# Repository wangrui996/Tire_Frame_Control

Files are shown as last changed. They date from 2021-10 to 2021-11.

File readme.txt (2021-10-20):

引脚分配
/********** 485通信 **************
PA2(USART2_TX)----------------485_RXD
PA3(USART2_RX)--------------- 485_TXD
PB8---------------------------------485_DIR

/********** 丝杠-86----驱动器 端口定义 **************
PE5------------------------------------------------------------DIR_OUT_2(丝杆方向)
PE6------------------------------------------------------------EN_OUT_2(86驱动器使能)
PC7 (TIM8_CH2)--------------------------------------------PUL_OUT_2(脉冲)

/********** 底盘-57----驱动器 端口定义 **************
PE3------------------------------------------------------------ DIR_OUT_1 
PE4------------------------------------------------------------ EN_OUT_1
PE11(TIM1_CH2)-------------------------------------------PUL_OUT_1

/********** 位移传感器**************
PA6(Timer3_CH1)------------------------------- WXY31_A_OUT编码器A相
PA7(Timer3_CH2)------------------------------- WXY31_B_OUT编码器B相

/********** 压力采样**************
PA5(ADC1_IN5)-----------------------------------DYLF_102_OUT

/********** 锂电池电压采样**************
PA4(ADC2_IN4)-----------------------------------Li_BATTERY_OUT

/********** 电机通断控制**************
PD8--------------------------------------- ----- ----MOTOR1_POWER_CTRL
PD9-------------------------------------------------MOTOR2_POWER_CTRL

编码器初始化。定时器设置上下拉问题
motor1.c    TIM_UpdateRequestConfig(TIM1,TIM_UpdateSource_Regular); /********* 设置只有计数溢出作为更新中断 ********/
motor1.c    TIM_SelectOnePulseMode(TIM8,TIM_OPMode_Single);/******* 单脉冲模式 **********/

上下位机通信说明-------485通信
需要发送的数据：压力值--保留两位小数---两位u8数据       整数部分最大150<255, 小数两位最大99<255
                锂电池电压--保留两位小数---两位u8数据   整数部分最大150<255, 小数两位最大99<255
				丝杠位移值（高度）----发送脉冲数，1000mm量程最大发送脉冲10000(0.1mm/脉冲)---两位u8数据
				速度--后面考虑
				RS485_TX_BUF[10]=[237, 13, 255, 240, 0, 0, 0, 0, 0, 0];

需要接收的数据：  0xED 
				  0x09 
				  0x57 
				  0x21
                  指令：1/2/3/4/5/6 
				  丝杠距离高位：
				  丝杠距离低位：
				  丝杠速度：				  
				  底盘距离高位：
				  底盘距离低位：
				  底盘速度：
				  0x57
				  0x20

嵌入式系统内部通信：信号量 
					消息邮箱  
					消息队列

电机控制  底盘：指定数目、指定频率脉冲发送-----考虑添加T型加减速算法
          丝杠：要有改变方向、频率的函数
		        读取编码器脉冲函数
				M法测速函数
				PID算法实现

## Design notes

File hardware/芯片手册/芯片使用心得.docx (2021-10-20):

1、 光耦6N137、、输入电阻，一般驱动发光二极管，电流10-20mA即可，若电压为3.3V，看手册二极管正向压降1.4V，电阻阻值在R=（3.3-1.4）➗（0.01-0.02）=95-190欧，因此用100R，180R都可。Proteus仿真结果，超过380R就不导通，380R时电流大概5mA。

HCPL-2531、6N137等光耦，输入输出端的电压大小要根据实际情况判断，接单片机一端应该是3V3，接外部电路可5V。

2、 发光二极管—看最大电流、，，电压---决定限流电阻阻值

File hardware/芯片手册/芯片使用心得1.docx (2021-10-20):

芯片封装下载网站 用户名为邮箱名

1、 光耦6N137、、输入电阻，一般驱动发光二极管，电流10-20mA即可，若电压为3.3V，看手册二极管正向压降1.4V，电阻阻值在R=（3.3-1.4）➗（0.01-0.02）=95-190欧，因此用100R，180R都可。Proteus仿真结果，超过380R就不导通，380R时电流大概5mA。

HCPL-2531、6N137等光耦，输入输出端的电压大小要根据实际情况判断，接单片机一端应该是3V3，接外部电路可5V。

光耦隔离的特点：实现信号的传递（单向），而两组信号件没有电气连接，两端实现完全的电隔离，因此两端不应共电源。（因为有些噪声会延着VCC或GND传播）

B0505S电源隔离模块，推荐电路见产品详情页或数据手册。

有些场合光耦可能实现电平转换的作用（可以不用三极管），此时可以共地。

2、 发光二极管—看最大电流、，，电压---决定限流电阻阻值
3、 485通信电路

SP3485芯片：

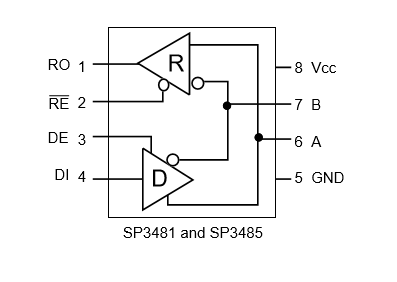
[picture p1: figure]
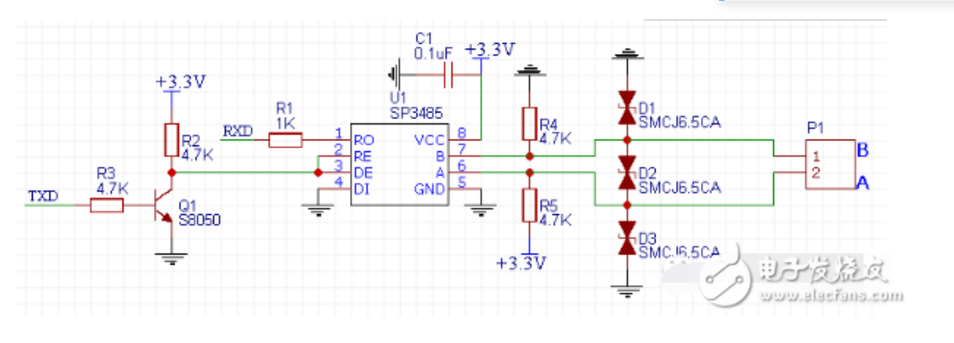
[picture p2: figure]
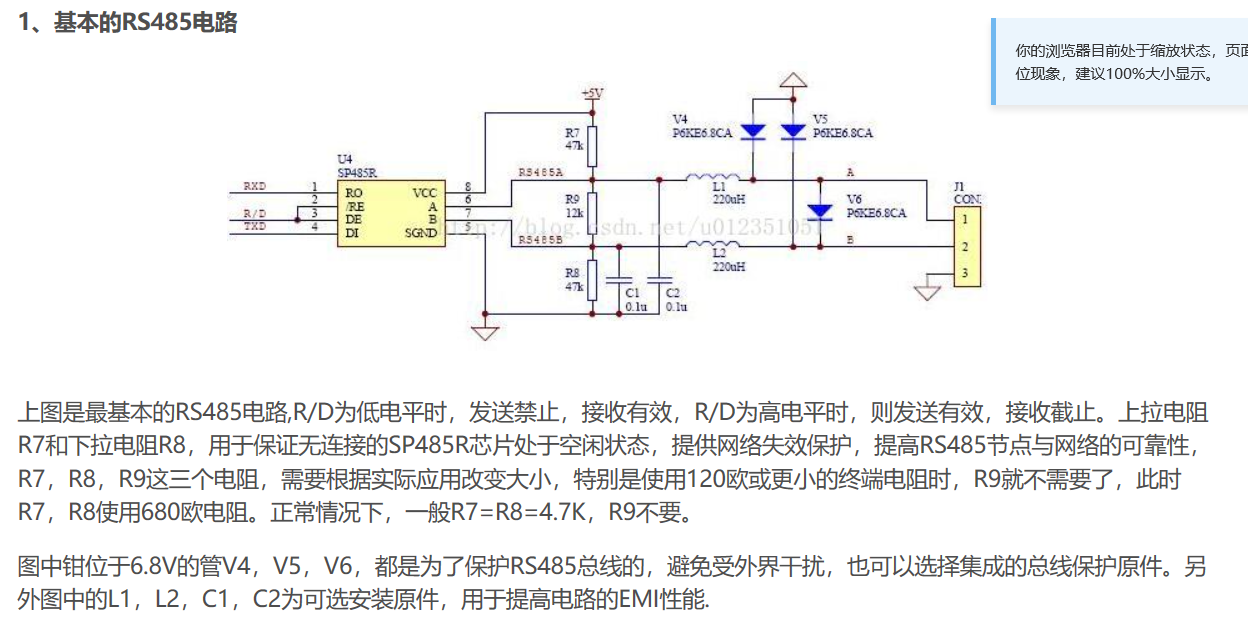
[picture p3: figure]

4、 电容应用类

滤波：

在设计电路板的时候，如果芯片没有特殊要求，需要把每个芯片旁边放上一个0.1微法电容。在PCB布线的时候，电容到电源引脚的距离最好在2mm以内。

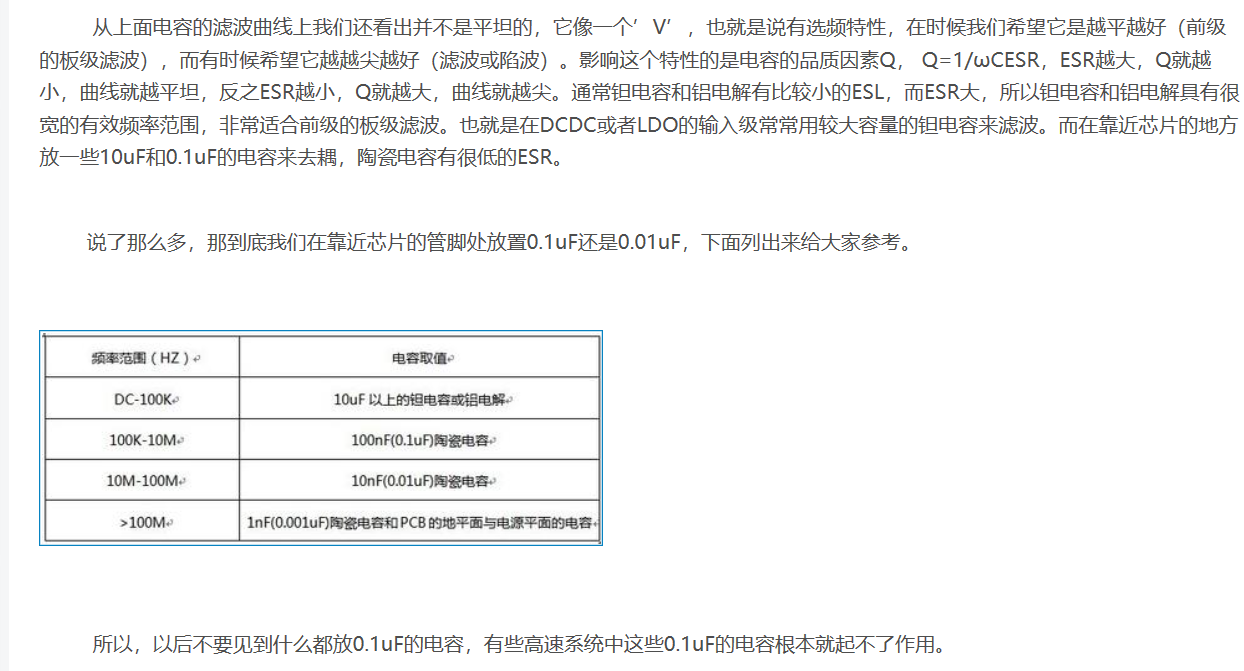
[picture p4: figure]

5、 继电器

单片机I/O口驱动能力有限、若继电器一端接地一端接I/O口，因为线圈自身电阻，单片机输出的电流不足以使触电吸合，，所以一般可用三极管如S8050方大驱动（可以用外部电压如5V、12V、24V）

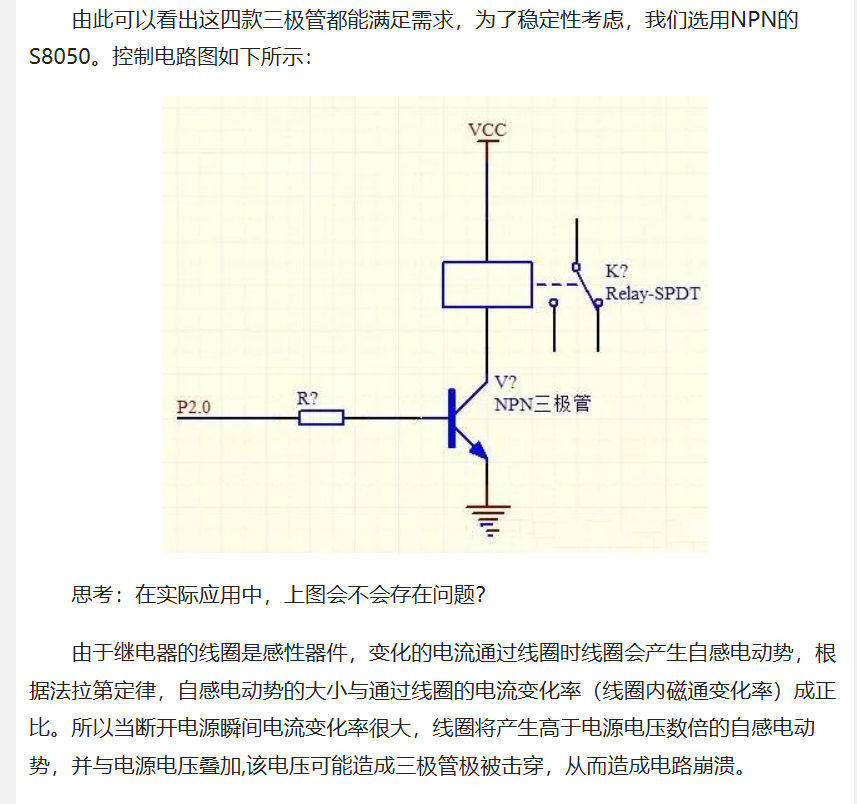
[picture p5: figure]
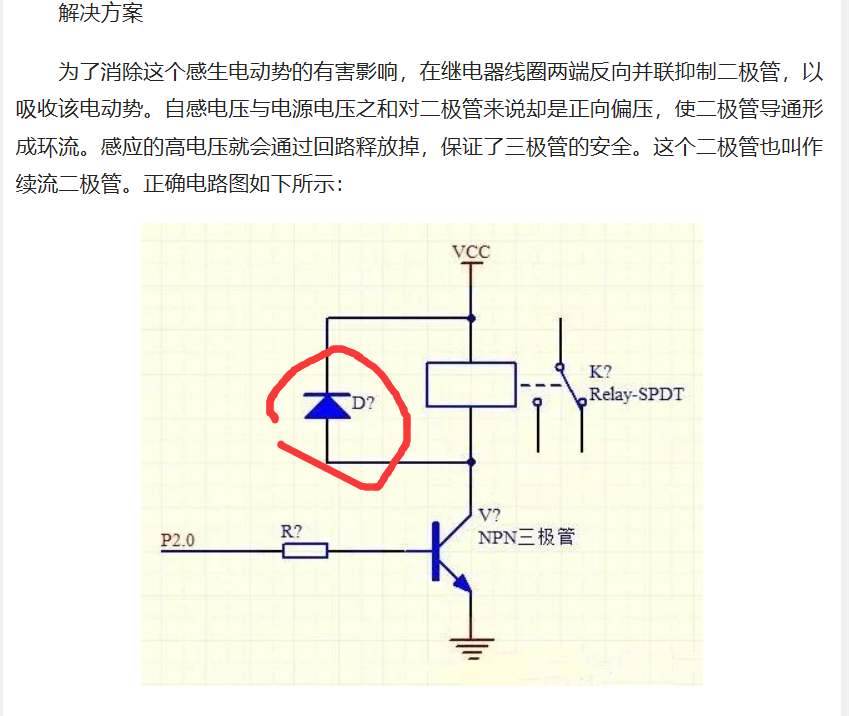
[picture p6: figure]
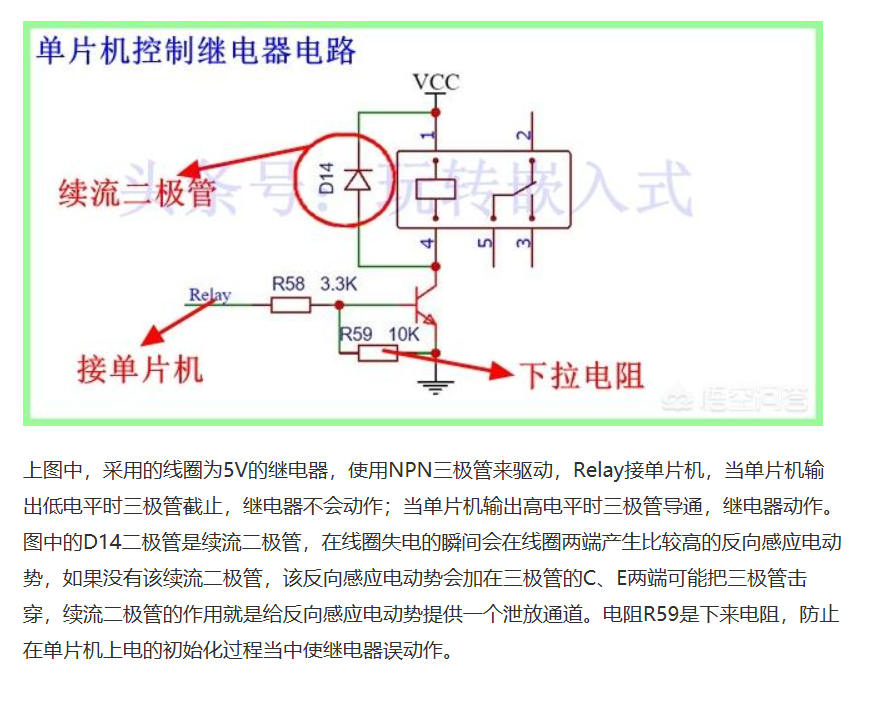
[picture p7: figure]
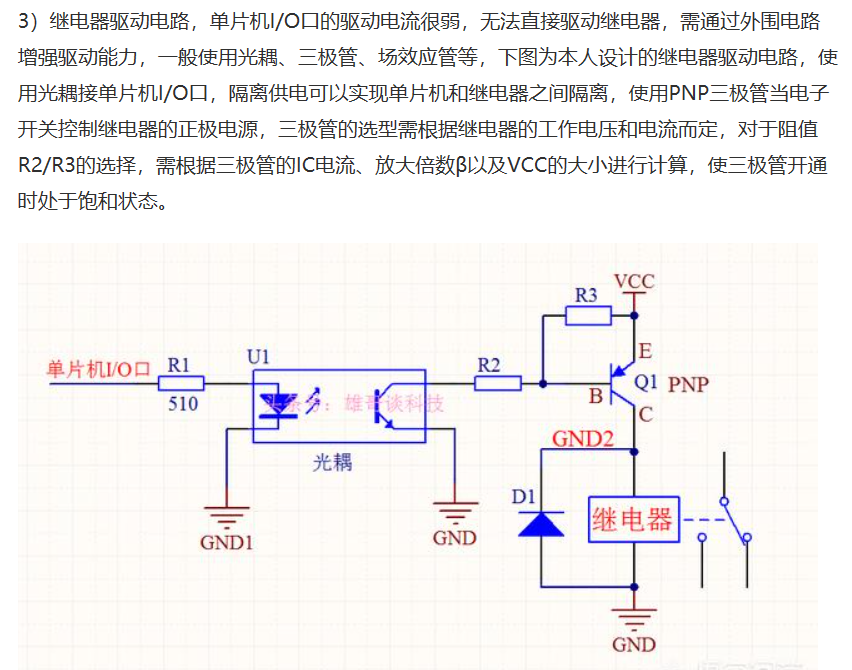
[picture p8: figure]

继电器：线圈电压怎么选，是多少？，继电器带负载能力多大，

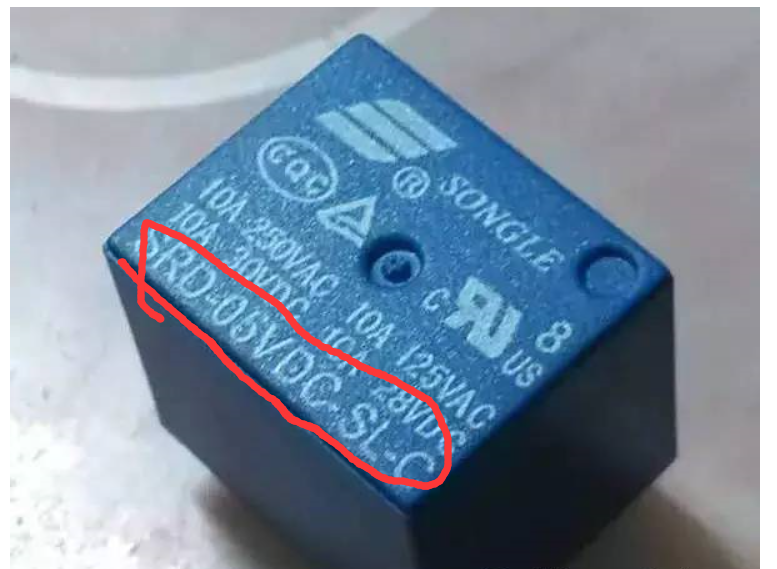
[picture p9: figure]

即可用让线圈通5V电，线圈即可吸合；

三极管：放大驱动继电器，其参数的选择？

6、 电源转换类：

5V-3.3V AMS1117

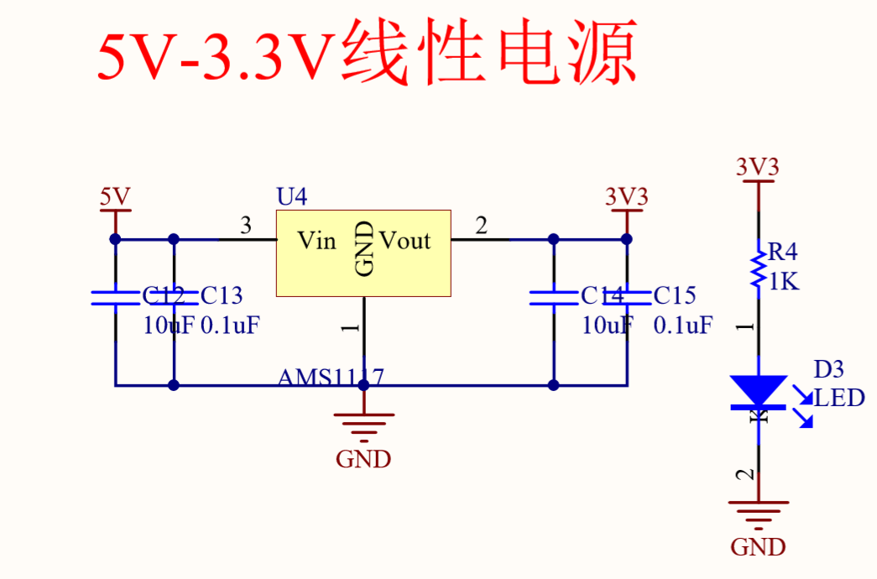
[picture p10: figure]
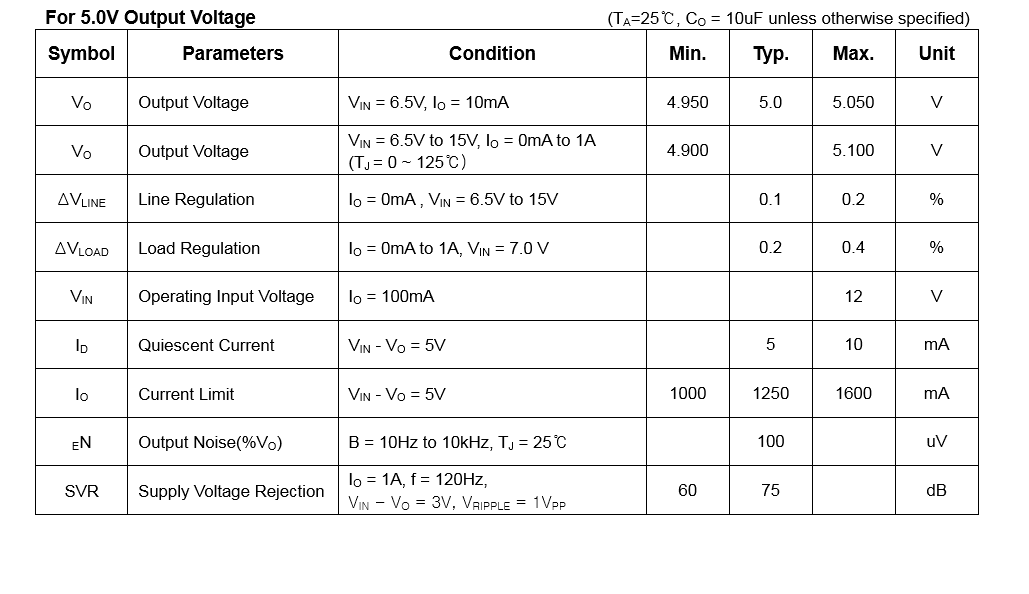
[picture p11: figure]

问题：

485电路的上下拉电阻阻值41K？、电感的大小、二极管为什么抗干扰（见第三条总结）？

位移传感器输入的电阻2K， ---换成500R，470R

继电器部分，R18的2.2K电阻怎样确定、U4光耦的VCC接的是几V？

C6和R17干啥的

继电器模块中，24V对地的滤波电容1uf？

485通信：的VCC和GND是不是也可以用隔离电源

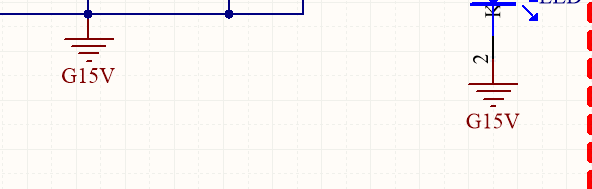
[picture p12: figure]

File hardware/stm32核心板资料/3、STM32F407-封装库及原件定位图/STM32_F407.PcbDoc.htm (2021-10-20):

Reporting Options

# File in Previous Format

Date | : | 2021/10/20
Time | : | 21:11:03
Filename | : | F:\STM32\最小系统板资料\3、STM32F407-封装库及原件定位图\STM32_F407.PcbDoc

Version | Warning
Release 12 | CAUTION - Air Gap Width previously controlled by Clearance rule is now controlled by Polygon Connect Style rule's newly introduced Air Gap Width (set to default value). Suggest reviewing each Polygon Connect Style rule's Air Gap Width attribute for correctness.
Release 13 | CAUTION - Silkscreen Over Component Pads Rules are converted to Silk To Solder Mask Clearance Rules. Suggest examining rule scopes for accuracy.

This file was generated by an earlier version of the software

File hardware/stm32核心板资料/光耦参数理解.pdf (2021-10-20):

长运通光电收集

# 光耦参数的理解

摘要：分析光耦各个指标参数的含义,以及日常设计中的注意事项,涉及 CTR 和延时。 关键字：光耦 CTR 延时

## 1 引言

光耦作为一个隔离器件已经得到广泛应用，无处不在。一般大家在初次接触到光耦时往

往感到无从下手，不知设计对与错，随着遇到越来越多的问题，才会慢慢有所体会。

本文就三个方面对光耦做讨论：光耦工作原理；光耦的 CTR 概念；光耦的延时。本讨论

也有认识上的局限性，但希望能帮助到初次使用光耦的同事。

## 1 理解光耦

光耦是隔离传输器件，原边给定信号，副边回路就会输出经过隔离的信号。对于光耦的

隔离容易理解，此处不做讨论。

以一个简单的图（图.1）说明光耦的工作：原边输入信号 Vin，施加到原边的发光二极

管和 Ri 上产生光耦的输入电流 If，If 驱动发光二极管，使得副边的光敏三极管导通，回路

VCC、RL 产生 Ic,Ic 经过 RL 产生 Vout，达到传递信号的目的。原边副边直接的驱动关联是

CTR（电流传输比），要满足 Ic≤If*CTR。

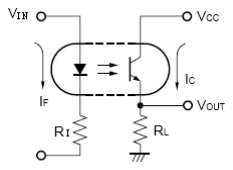
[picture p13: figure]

图.1

光耦一般会有两个用途：线性光耦和逻辑光耦，如果理解？

工作在开关状态的光耦副边三极管饱和导通，管压降<0.4V，Vout 约等于 Vcc（Vcc-0.4V

左右），Vout 大小只受 Vcc 大小影响。此时 Ic<If*CTR，此工作状态用于传递逻辑开关信号。

工作在线性状态的光耦，Ic=If*CTR，副边三极管压降的大小等于 Vcc-Ic*RL，Vout= Ic*RL

=(Vin-1.6V)/Ri * CTR*RL，Vout 大小直接与 Vin 成比例，一般用于反馈环路里面 (1.6V 是

粗略估计，实际要按器件资料，后续 1.6V 同) 。

对于光耦开关和线性状态可以类比为普通三极管的饱和放大两个状态。

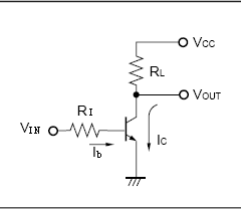
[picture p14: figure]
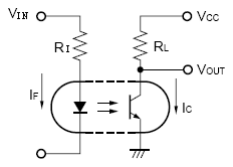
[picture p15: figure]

所以通过分析实际的电路，除去隔离因素，用分析三极管的方法来分析光耦是一个很有

效的方法。此方法对于后续分析光耦的 CTR 参数，还有延迟参数都有助于理解。

### 2 光耦 CTR

概要：1)对于工作在线性状态的光耦要根据实际情况分析；2)对于工作在开关状态的光

耦要保证光耦导通时 CTR 有一定余量；3)CTR 受多个因素影响。

## 2.1 光耦能否可靠导通实际计算

举例分析，例如图.1 中的光耦电路，假设 Ri = 1k,Ro = 1k,光耦 CTR= 50%，光耦导通

时假设二极管压降为 1.6V，副边三极管饱和导通压降 Vce=0.4V。输入信号 Vi 是 5V 的方波，

输出 Vcc 是 3.3V。Vout 能得到 3.3V 的方波吗？

我们来算算：If = (Vi-1.6V)/Ri = 3.4mA

副边的电流限制：Ic’ ≤ CTR*If = 1.7mA

假设副边要饱和导通，那么需要 Ic’ = (3.3V – 0.4V)/1k = 2.9mA，大于电流通道限

制，所以导通时，Ic 会被光耦限制到 1.7mA， Vout = Ro*1.7mA = 1.7V

比较项目 | | 光耦 | | 三极管

电路图

前级电流 | If(=(Vin-1.6)/Ri) | | Ib(=(Vin-0.6)/Ri)
电流限制条件 | Ic ≤ CTR*If | | Ic ≤β* Ib
| 理解：If 确定，光耦副边电流通道大小 确定，实际的 Ic 不能大于该通道 | | 理解：Ib 确定，三极管副边电流通道大 小确定，实际的 Ic 不能大于该通道
饱和/开关状态 | 当 RL阻值大时，Vcc/RL < CTR*If 光耦导通时，Vout ~= 0 V | | 当 RL阻值大时，Vcc/RL <β* Ib 三极管导通时，Vout ~= 0 V
放大/线性状态 | 当 RL阻值小时，Vcc/RL > CTR*If 此时，光耦副边会提高光敏三极管的导 通压降，限制实际的 Ic 在电流通道内 (Ic = CTR*If)。光耦导通时，Vout 输 出大小与 Vin 有线性关系。 | | 当 RL阻值小时，Vcc/RL >β* Ib 此时，三极管会提高管压降，限制实际 的 Ic 在电流通道内(Ic =β* Ib)。三 极管导通时，Vout 输出大小与 Vin 有线 性关系。

所以副边得到的是 1.7V 的方波。

为什么得不到 3.3V 的方波，可以理解为图.1 光耦电路的电流驱动能力小，只能驱动

1.7mA 的电流，所以光耦会增大副边三极管的导通压降来限制副边的电流到 1.7mA。

解决措施：增大 If；增大 CTR；减小 Ic。对应措施为：减小 Ri 阻值；更换大 CTR 光耦；

增大 Ro 阻值。

将上述参数稍加优化，假设增大 Ri 到 200 欧姆，其他一切条件都不变，Vout 能得到 3.3V

的方波吗？

重新计算：If = (Vi – 1.6V)/Ri = 17mA；副边电流限制 Ic’ ≤ CTR*If = 8.5mA，远

大于副边饱和导通需要的电流(2.9mA)，所以实际 Ic = 2.9mA。

所以，更改 Ri 后，Vout 输出 3.3V 的方波。

开关状态的光耦，实际计算时，一般将电路能正常工作需要的最大 Ic 与原边能提供的

最小 If 之间 Ic/If 的比值与光耦的 CTR 参数做比较，如果 Ic/If ≤CTR，说明光耦能可靠

导通。一般会预留一点余量（建议小于 CTR 的 90%）。

工作在线性状态令当别论。

## 2.2 CTR 受那些因素影响

上一节说到设计时要保证一定 CTR 余量。就是因为 CTR 的大小受众多因素影响，这些因

素之中既有导致 CTR 只离散的因素（不同光耦），又有与 CTR 有一致性的参数（壳温/If）。

1)光耦本身：以 8701 为例，CTR 在 Ta=25℃/If=16mA 时，范围是(15%~35%)
说明 8701 这个型号的光耦，不论何时/何地，任何批次里的一个样品，只要在 Ta=25℃ /If=16mA 这个条件下，CTR 是一个确定的值，都能确定在 15%~35%以内。 计算导 通时，要以下限进行计算，并且保证有余量。计算关断时要以上限。 2)壳温影响：

Ta=25℃条件下的 CTR 下限确定了，但往往产品里面温度范围比较大，比如光耦会工作

在（-5~75℃）下，此种情况下 CTR 怎么确定？还是看 8701 的手册：有 Ta-CTR 关系图：

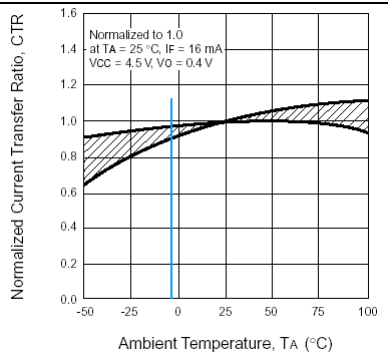
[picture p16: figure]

从图中看出，以 25 度的为基准，在其他条件不变的情况下，-5 度下的 CTR 是 25 度下

的 0.9 倍左右，75 度下最小与 25 度下的 CTR 持平。

所以在 16mA/(-5~75℃)条件下，8701 的 CTR 最小值是 15%*0.9 = 13.5%

3) 受 If 影响。

假设如果实际的 If 是 3.4mA，那么如何确定 CTR 在 If=3.4mA / Ta=(-5~75℃)条件下的

最小 CTR 值。

查看 8701 的 If-CTR 曲线。图中给出了三条曲线，代表抽取了三个样品做测试得到的

If-CTR 曲线，实际只需要一个样品的曲线即可。

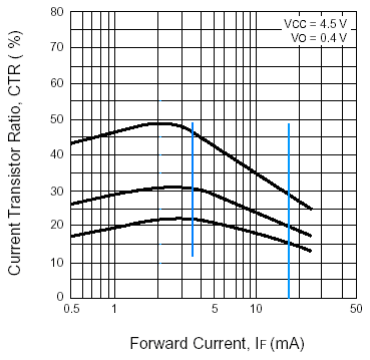
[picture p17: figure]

注：此图容易理解为下限/典型/上限三个曲线，其实不然。大部分图表曲线只是一个相

对关系图，不能图中读出绝对的参数值。

计算：选用最上面一条样品曲线，由图中查出，If=16mA 时 CTR 大概 28%，在 If=3.4mA

时 CTR 大概在 46%。3.4mA 是 16mA 时的 46%/28% = 1.64 倍；

所以，在 If=3.4mA / (-5~75℃)，CTR 下限为 13.5% * 1.64 = 22.2%

以上所有分析都是基于 8701 的，其他光耦的特性曲线需要查用户手册，分析方法一样。

## 3 光耦延时

上述 CTR 影响到信号能不能传过去的问题，类似于直流特性。下面主要分析光耦的延时

特性，即光耦能传送多快信号。

涉 及到 两个参 数： 光耦导通延时 tplh 和 光耦关断 延时 tphl ，以 8701 为例 ：在

If=16mA/Ic=2mA 时候，关断延时最大 0.8uS，导通延时最大 1.2uS。所以用 8701 传递 500k

以上的开关信号就需要不能满足。

下图是一个实测的延时波形（ch4 原边（红），ch2 副边（绿））

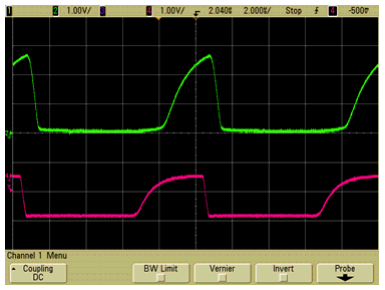
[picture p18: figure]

图.2
对于 tp 参数的设计更应该考虑余量，因为 tp 参数也受其他因素影响较多。
1) 受温度影响
8701 的 Ta-If 特征曲线：温度升高，开关延时都会增大。

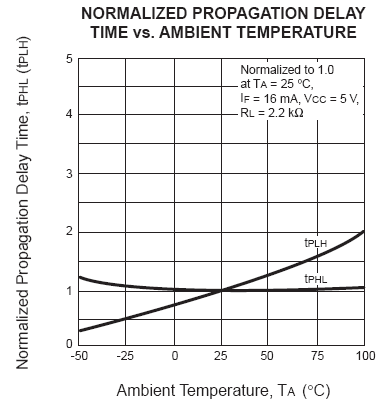
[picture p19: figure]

图.3
2) 受原边 If 大小影响
8701 的 tp-If 特征曲线：If 增大，关断延时减小，开通延时增大

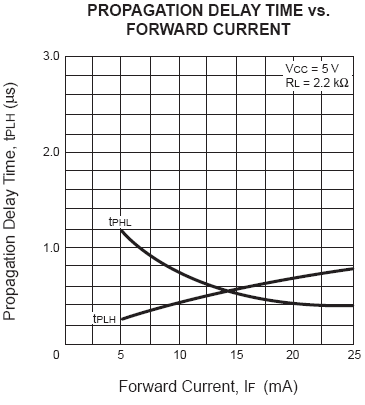
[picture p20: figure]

图.4
3) 受副边 Ic 大小影响
8701 的 tp-RL 特征曲线：RL 减小，导通延时增大明显

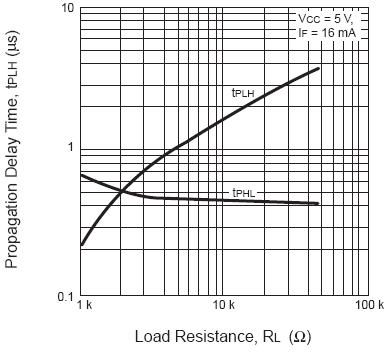
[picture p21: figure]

图.5
针对具体电路的特点，计算最大延时时也是采用与 CTR 一样的方法，通过器件资料给 定特定环境下的准确范围，然后逐一通过三个曲线确定具体电路下的光耦最大延时。

注：同一个型号的光耦 CTR/延时特性是一致的，不同光耦的延时特性不尽相同，所以 需要根据所用光耦的用户手册来确定。

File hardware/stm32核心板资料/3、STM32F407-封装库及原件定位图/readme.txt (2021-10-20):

本文件夹包含AD版本的封装库,大家根据自己的需要选择.我们不提供PROTEL之外的其他PCB软件封装库,请见谅.

	       	出品：   嵌入式开发网 
                         mcudev.taobao.com

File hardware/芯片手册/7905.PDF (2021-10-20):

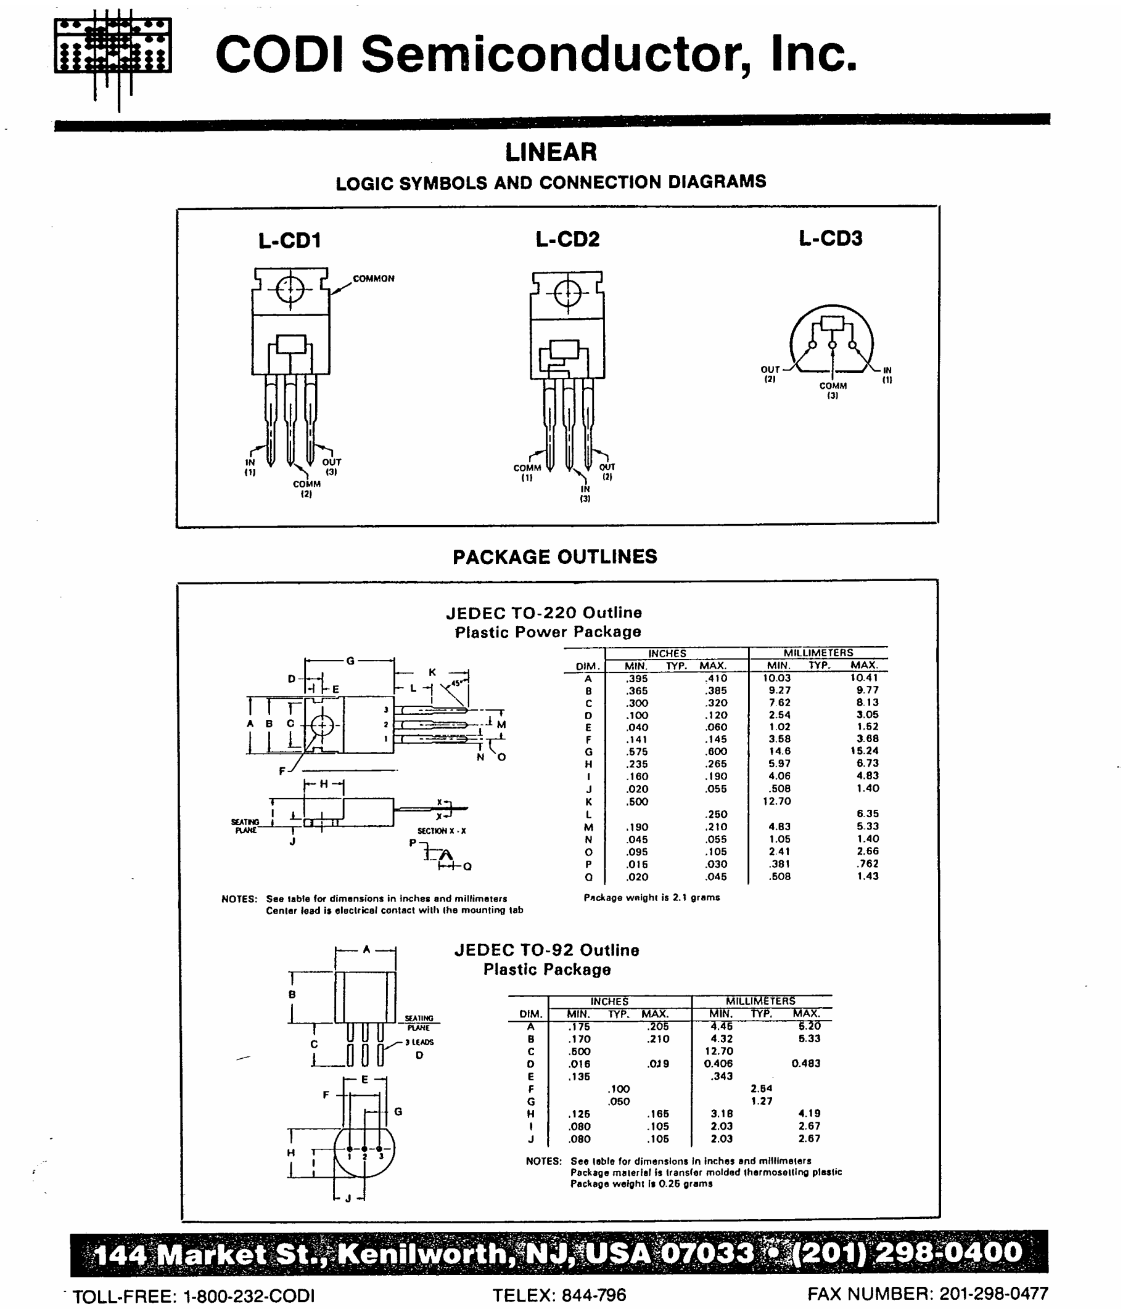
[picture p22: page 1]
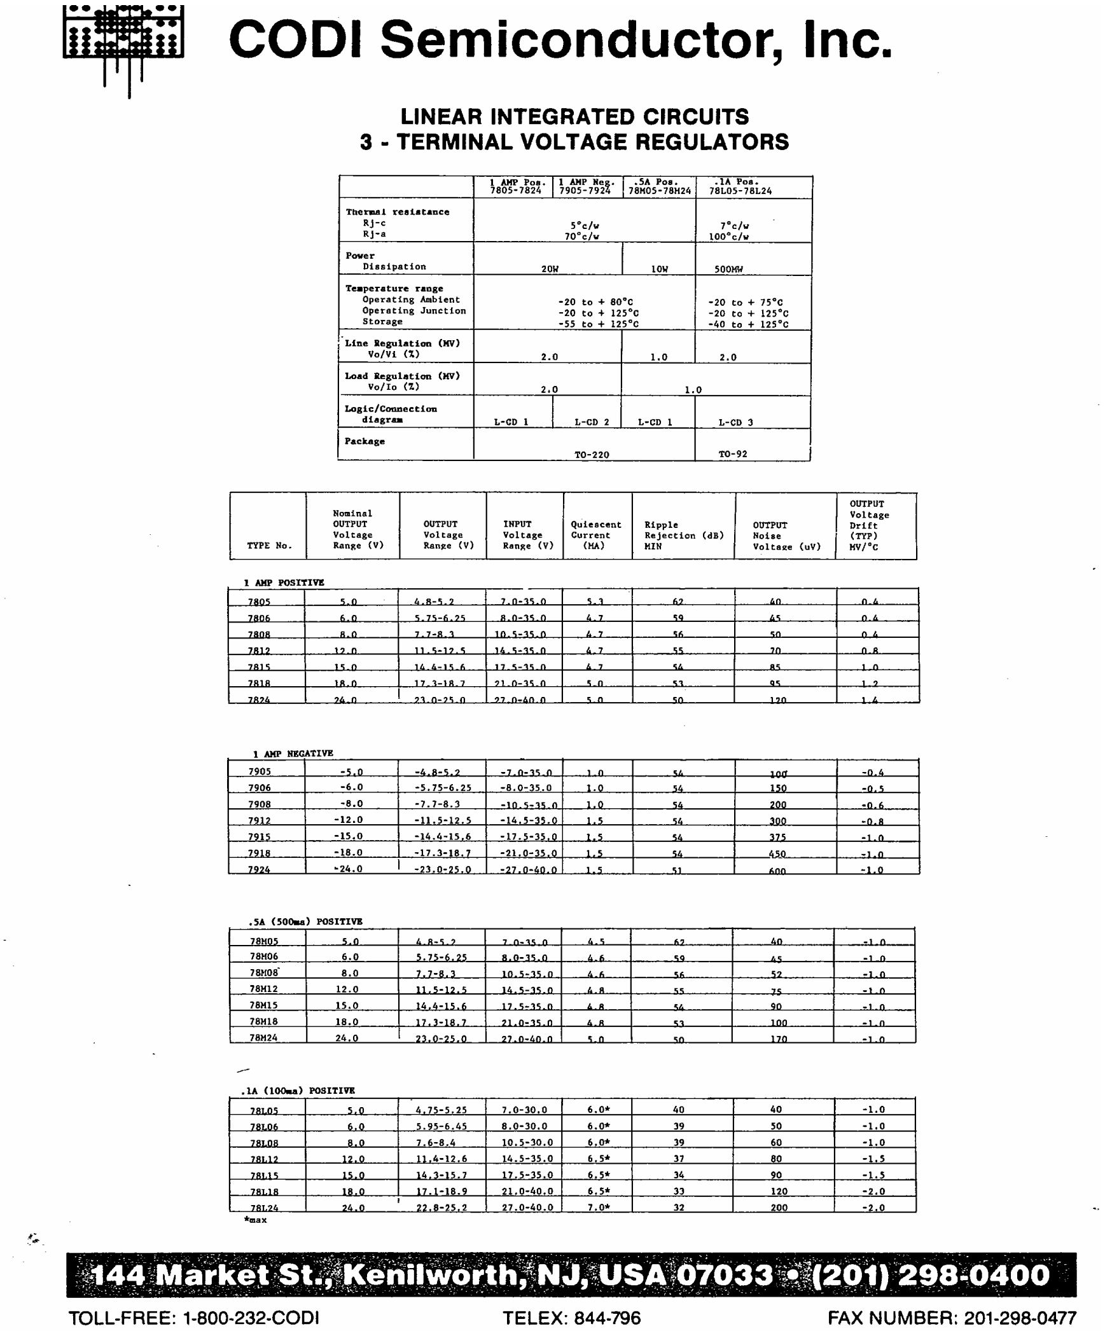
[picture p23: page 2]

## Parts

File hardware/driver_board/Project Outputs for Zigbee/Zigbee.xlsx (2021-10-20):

Comment | Description | Designator | Footprint | LibRef | Quantity | 购买链接 | 备注
F407VGT6底座封装 |  | 1 | F407VGT6底座封装 | F407VGT6底座封装 | 1
1uF | Capacitor | C6, C8, C11, C12 | 0603_C | CAP | 4 | https://item.taobao.com/item.htm?spm=a1z10.3-c-s.w4002-18137167944.16.2e192ec8RxSewg&id=530610812107 | 电阻电容直接买一个包就行
0.1uF | Capacitor | C13 | 0603_C | CAP | 1
LED | LED 发光二极管 | D1, D2, D3, D4, D6, D7, D10, D11, D15, D16 | 0603_LED | LED | 10 | https://item.taobao.com/item.htm?spm=a1z10.3-c-s.w4002-18137167944.15.dc9c2ec8fDyNGL&id=525875387129 | LED也是一个包各种颜色都有
LED红 | LED 发光二极管 | D5, D12 | 0603_LED | LED | 2
MMBD7000 |  | D9, D14 | SOT23 | MMBD7000 | 2 | https://item.taobao.com/item.htm?spm=a1z10.3-c-s.w4002-18137167944.9.618d2ec85Wt529&id=611336762473
holes |  | H1, H2, H3, H4 | 铜柱（小焊盘） | 铜柱 | 4
COM_2 |  | J1, J2, J3, J4, J5, J6, J7, J8, J9, J10, J11, J12, J13, J14, J15 | 5.08A-2PIN | COM_2 | 15 | https://item.taobao.com/item.htm?spm=a1z10.3-c-s.w4002-18137167944.12.22982ec8x13a8i&id=538793070757
header |  | JP6 | 5.08A-3PIN | HEADER 3 | 1
OJ-SS-124HM2 |  | K1, K2 | G4A-1A-PE-24V | OJ-SS-124HM2 | 2 | https://item.taobao.com/item.htm?spm=a1z09.2.0.0.40a52e8dBBcYpT&id=20355564384&_u=l1k54e5p1c41
NPN2 | 贴片 | Q1, Q2 | SOT-23-3 | NPN2 | 2 | https://item.taobao.com/item.htm?spm=a1z10.3-c-s.w4002-18137167944.21.6c652ec8VVapCy&id=611258987843
20K | Resistor | R1 | 0603_R | RES | 1
2K | Resistor | R2, R3, R13, R14, R17, R25, R31, R35 | 0603_R | RES | 8
10K | Resistor | R4 | 0603_R | RES | 1 | https://item.taobao.com/item.htm?spm=a1z10.3-c-s.w4002-18137167944.12.515b2ec820JMOL&id=530584393475 | 电阻电容单买也行，就是要一个一个找，都在一家店 (https://item.taobao.com/item.htm?spm=a1z10.3-c-s.w4002-18137167944.12.515b2ec820JMOL&id=530584393475)
180R | Resistor | R5, R6, R10, R16, R19, R23 | 0603_R | RES | 6
100K | Resistor | R7 | 0603_R | RES | 1
1K | Resistor | R8, R9, R12, R20, R21, R22, R27, R28, R32, R38 | 0603_R | RES | 10
5K | Resistor | R11 | 0603_R | RES | 1
470R | Resistor | R15, R24 | 0603_R | RES | 2
2.2K | Resistor | R18, R26 | 0603_R | RES | 2
4.7K | Resistor | R29, R30 | 0603_R | RES | 2
100R | Resistor | R33, R34, R37 | 0603_R | RES | 3
120R | Resistor | R36 | 0603_R | RES | 1
HCPL-2531 |  | U1, U3, U7 | SOP8 | HCPL-2531 | 3 | https://item.taobao.com/item.htm?spm=a1z10.3-c-s.w4002-18137167944.9.c8e62ec8I7sJBd&id=534341592457
6N137 |  | U2, U5 | SOP8 | 6N137 | 2 | https://item.taobao.com/item.htm?spm=a1z10.3-c-s.w4002-18137167944.9.7b1b2ec8Sd4msu&id=534092834069
TLP185 |  | U4, U6 | SOP4 | TLP184 | 2 | https://item.taobao.com/item.htm?spm=a1z10.3-c-s.w4002-18137167944.9.5d642ec8Y6uTDr&id=597007341875
MAX485ESA |  | U8 | SOP8 | MAX485ESA | 1 | https://item.taobao.com/item.htm?spm=a1z10.3-c-s.w4002-18137167944.9.55722ec8YVXSXd&id=527232535941

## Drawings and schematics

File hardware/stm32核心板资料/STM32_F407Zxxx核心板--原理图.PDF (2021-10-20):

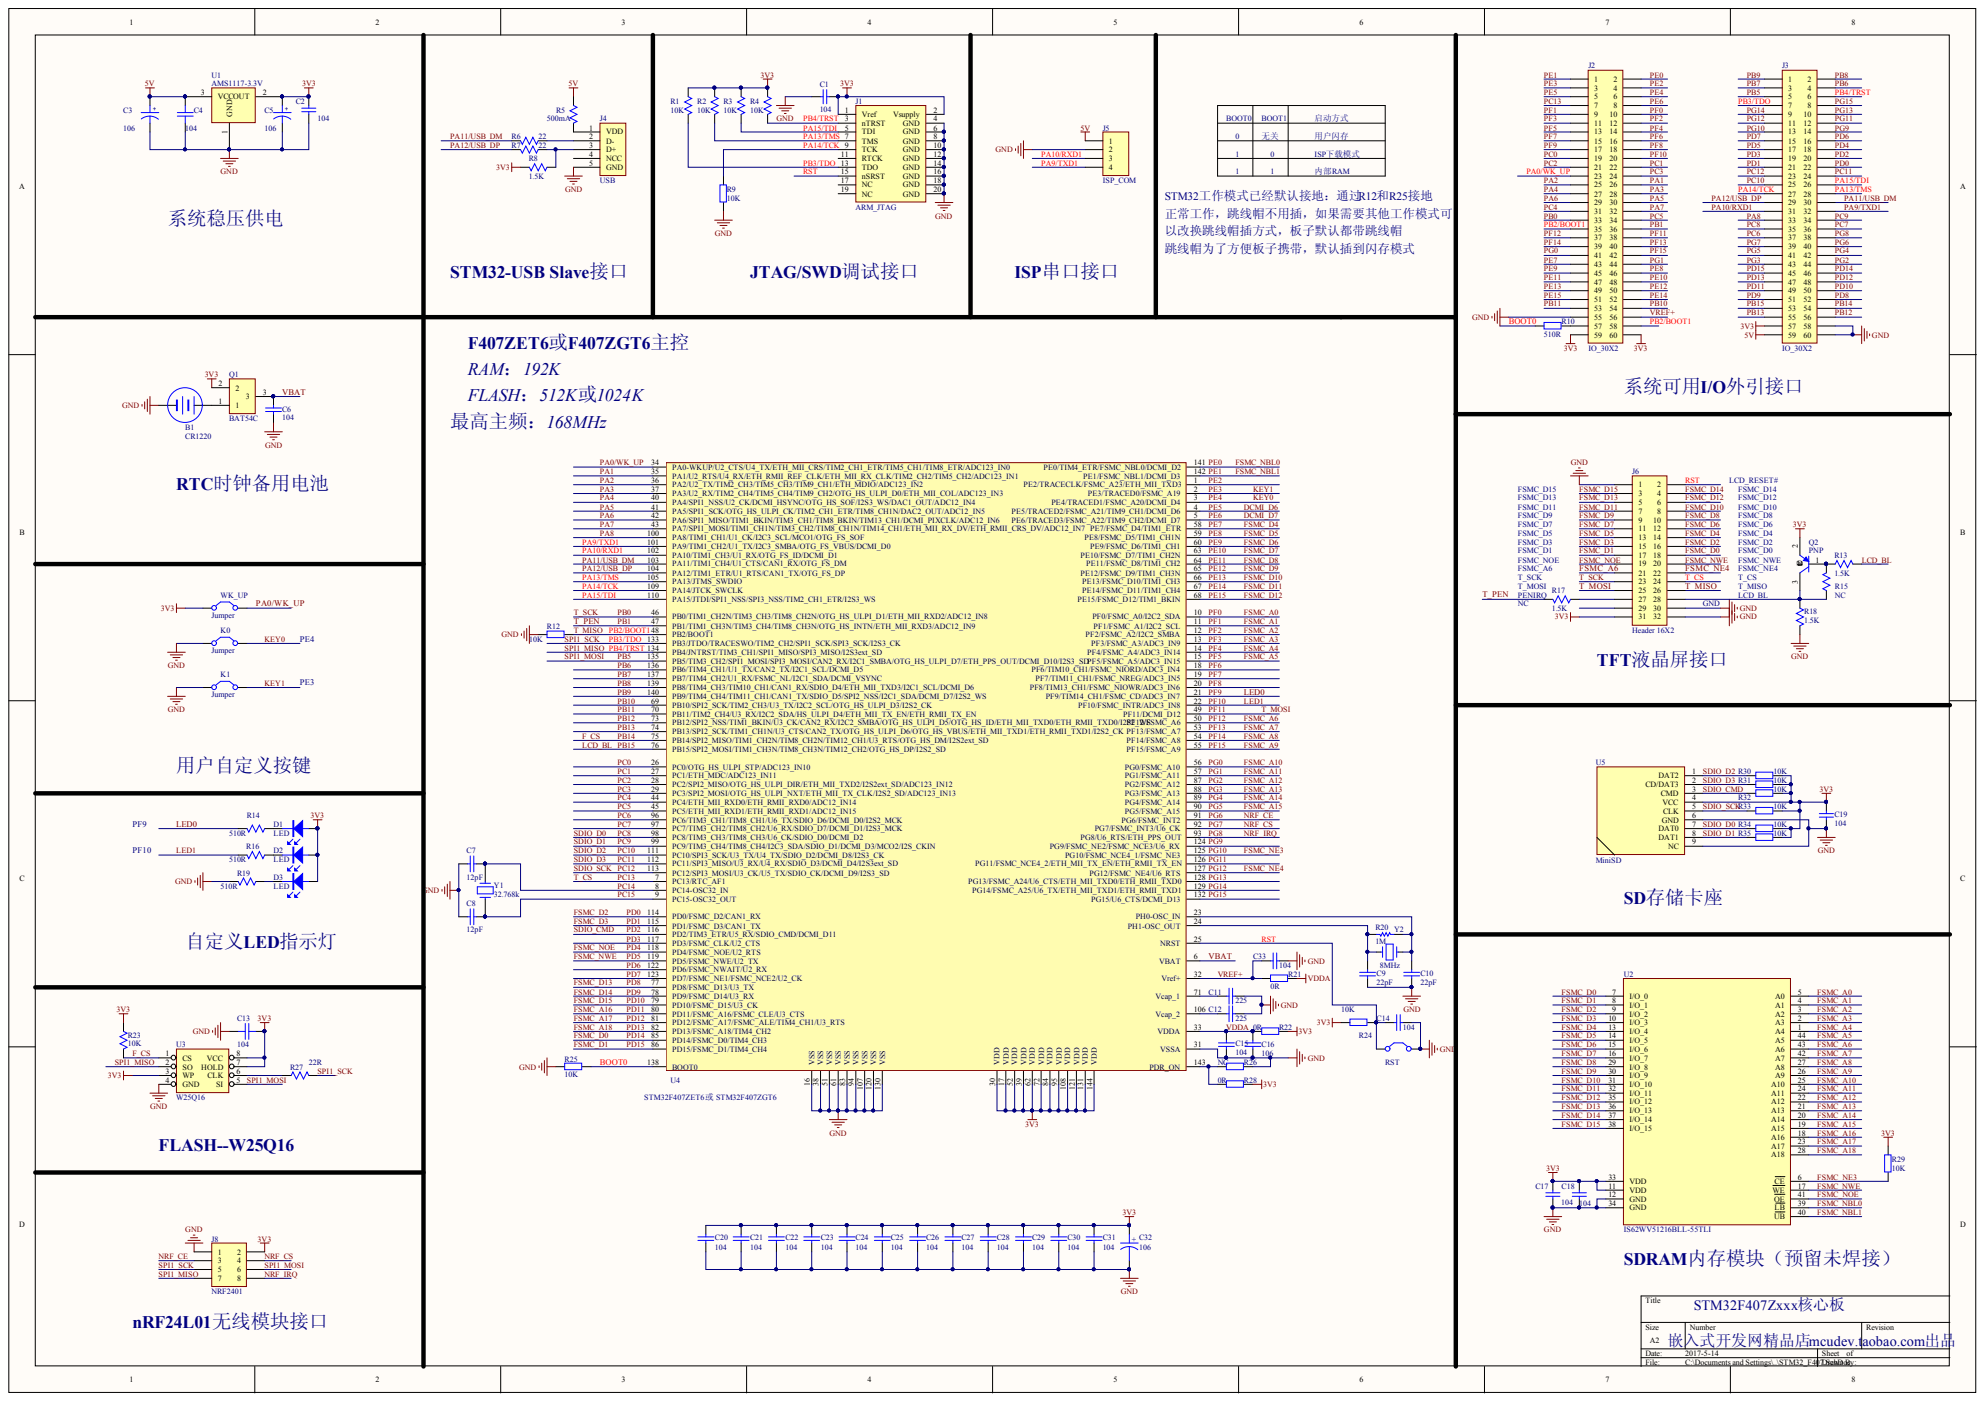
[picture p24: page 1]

PA15/TDI PB3/TDO PB4/TRST RST

VRE F + | 8MHz C 9

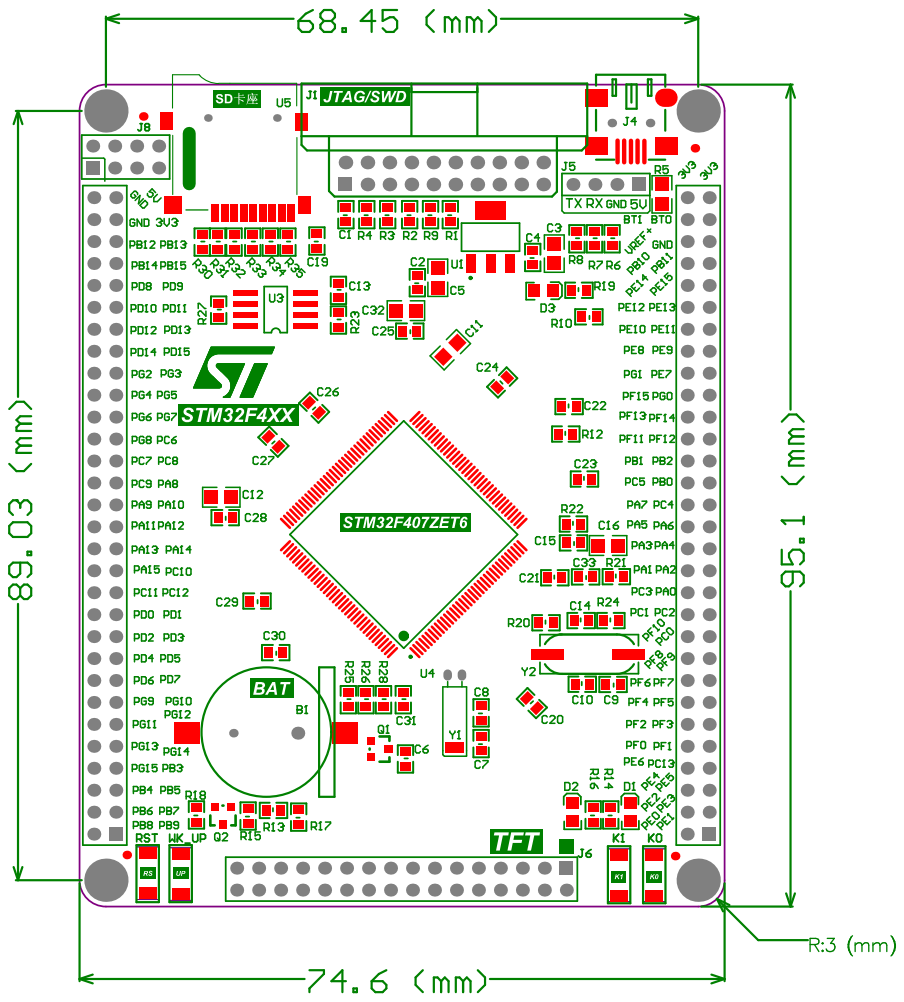
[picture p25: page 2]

Bill of Materials | <Parameter Title not found>
Source Data From: | STM32_F407.PrjPCB
Project: | | STM32_F407.PrjPCB
Variant: | | None
Creation Date: 2017-5-14 | 16:17:47
Print Date: | 42869 | 42869.67907
Footprint | Comment | LibRef | Designator | Description | Quantity
CP1220 | CR1220 | BATTERY | B1 | 1
RC0603 | 104 | Cap, Cap, CAP,
CAP, CAP, CAP,
CAP, Cap, Cap,
Cap Semi, CAP,
CAP, CAP, CAP,
CAP, CAP, CAP,
CAP, CAP, CAP,

## CAP, CAP, CAP

C1, C2, C4, C6, C13, C14, C15, C17, C18, C19, C20, C21, C22, C23, C24, C25, C26,

## C27, C28, C29, C30, C31, C33

Capacitor, Capacitor, [NoValue], Capcitor, [NoValue], Capcitor, Capcitor, Capacitor,

## Capacitor, Capacitor (Semiconductor SIM

Model), Capcitor, Capcitor, Capcitor, Capcitor, Capcitor, Capcitor, Capcitor, Capcitor, Capcitor, Capcitor, Capcitor,

## Capcitor, Ca

23

RC0805 | 106 | CAP2, CAP2,
CAP,

## CAPACITOR POL

C3, C5, C16, C32 | [NoValue], [NoValue], Capcitor, Capacitor | 4
RC0603 | 12pF | CAP | C7, C8 | Capcitor | 2
RC0603 | 22pF | CAP | C9, C10 | Capcitor | 2
RC0805 | 225 | CAP | C11, C12 | Capcitor | 2
LED0805 | LED | LED | D1, D2, D3 | | 3
JTAG20P | ARM_JTAG | JTAG | J1 | JTAG | 1
IDE2X30 | IO_30X2 | Header 30X2 | J2, J3 | Header, 30-Pin, Dual row | 2
MINUSB | USB | usb | J4 | | 1
HDR1X4 | ISP_COM | Header 4 | J5 | Header, 4-Pin | 1
IDE2X16-2.54Header 16X2 | Header 16X2 | J6 | Header, 16-Pin, Dual row | 1
DIP2X4-2.54 | NRF2401 | Header 4X2 | J8 | Header, 4-Pin, Dual row | 1
key | Jumper | Jumper | K0, K1, WK_UP | Jumper Wire | 3
BAT54C | BAT54C | BAT54C | Q1 | | 1
PNP_SOT23 | PNP | PNP | Q2 | PNP Bipolar Transistor | 1
RC0603 | 10K | RES, RES, RES,
| | RES, Res2,
| | Res2, RES,
| | Res2, Res2,
| | Res2, Res2,
| | Res2, Res2,
| | Res2, Res2,
| | Res2

R1, R2, R3, R4, R9, R12, R23, R24, R25,

## R29, R30, R31, R32, R33, R34, R35

[NoValue], [NoValue], [NoValue], [NoValue], Resistor, Resistor, [NoValue], Resistor, Resistor, Resistor, Resistor, Resistor,

## Resistor, Resistor, Resistor, Resistor

16

RC0805 | 500mA | RES | R5 | | 1
RC0603 | 22 | RES | R6, R7 | | 2
RC0603 | 1.5K | RES | R8, R13, R17, R18 | | 4
RC0603 | 510R | Res2, RES,
| | RES, RES | R10, R14, R16, R19 | Resistor, [NoValue], [NoValue], [NoValue] | 4
RC0603 | NC | RES, Res2 | R15, R26 | [NoValue], Resistor | 2
RC0603 | 1M | Res1 | R20 | Resistor | 1
RC0603 | 0R | Res2 | R21, R22, R28 | Resistor | 3
RC0603 | 22R | RES | R27 | | 1
key | Key | Jumper | RST | Jumper Wire | 1
SOT223 | AMS1117-3.3V | 11 | U1 | | 1
TSOP44 | IS62WV51216BL
| L-55TLI

## IS62WV51216BL

| | L-55TLI | U2 | | 1
SOIC8P | W25Q16 | W25X16 | U3 | | 1
LQFP144N | STM32F407ZET
| 6 或

## STM32F407ZGT

| 6

## STM32F407ZET

| | 6 | U4 | STM32F407ZET6 | 1
TF_SD | MiniSD | MiniSD | U5 | | 1
32.768k | 32.768k | CRYSTAL | Y1 | Crystal 8MHz PLUG | 1
SMD49S | 8MHz | XTAL | Y2 | Crystal Oscillator | 1
| | | | | 91
Approved | | Notes

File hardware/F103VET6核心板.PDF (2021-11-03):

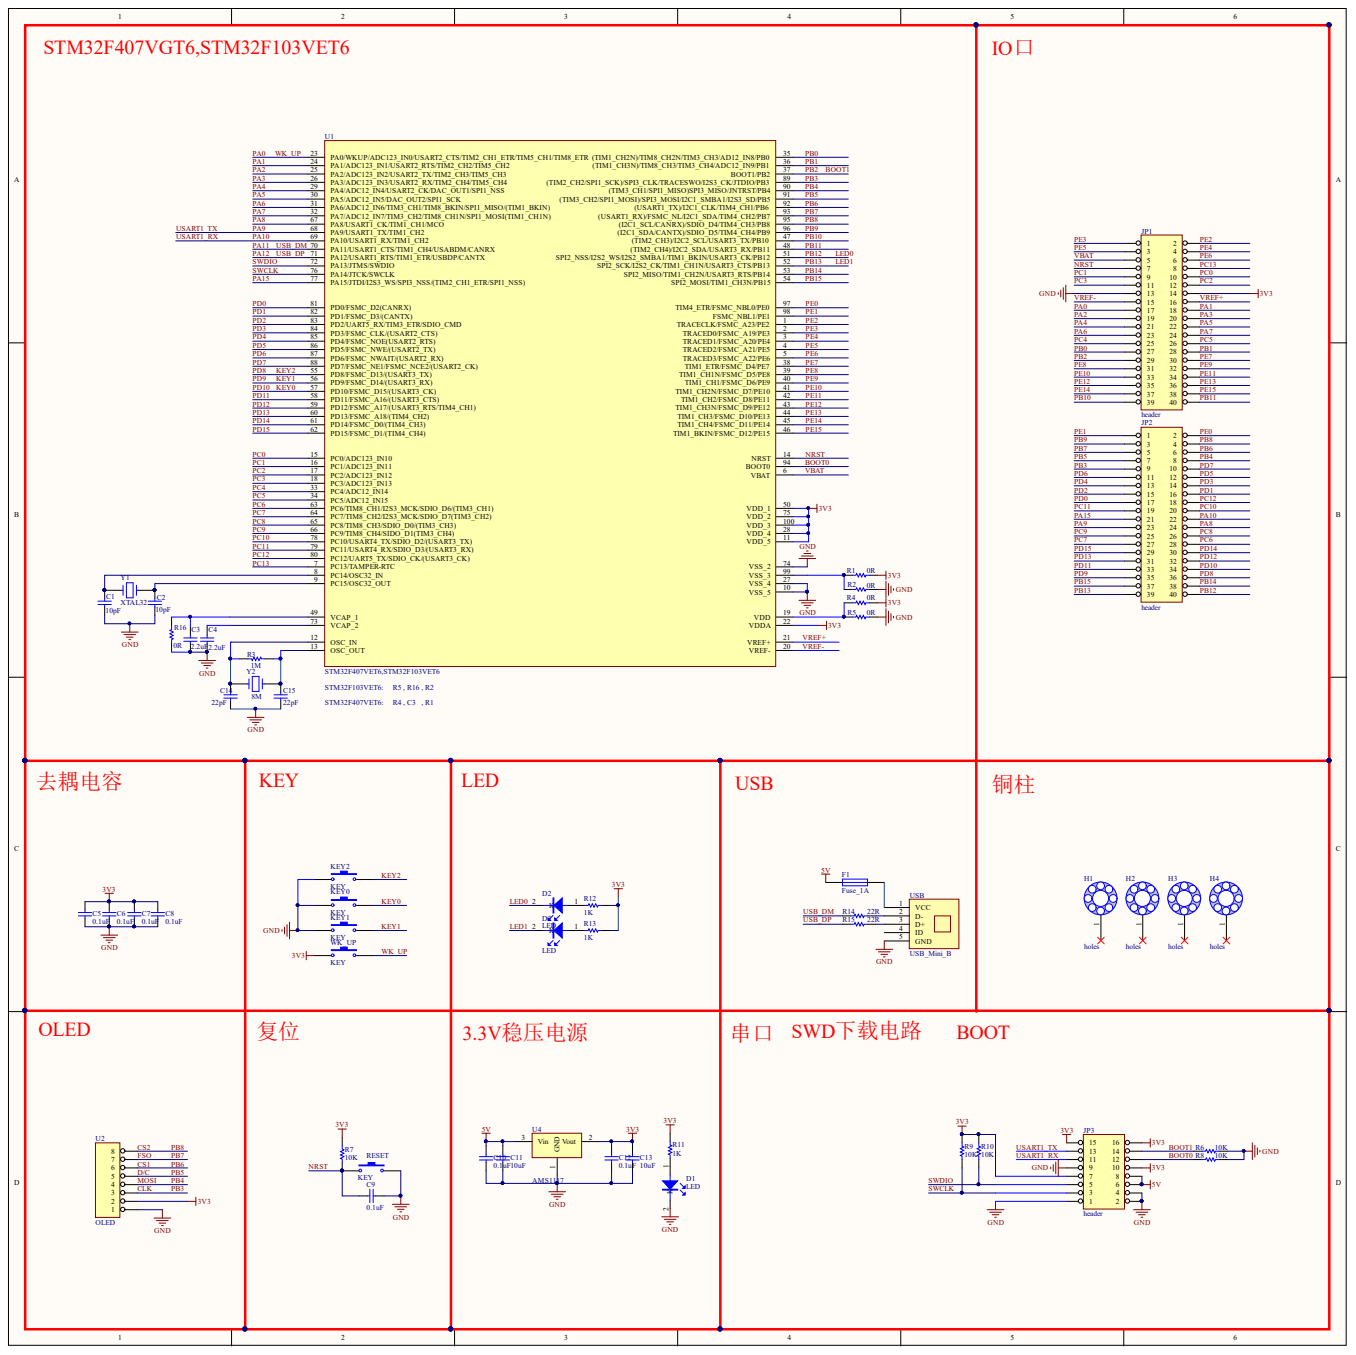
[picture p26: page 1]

VREF- | VREF+

8M | OSC_OUT 13 | VREF-

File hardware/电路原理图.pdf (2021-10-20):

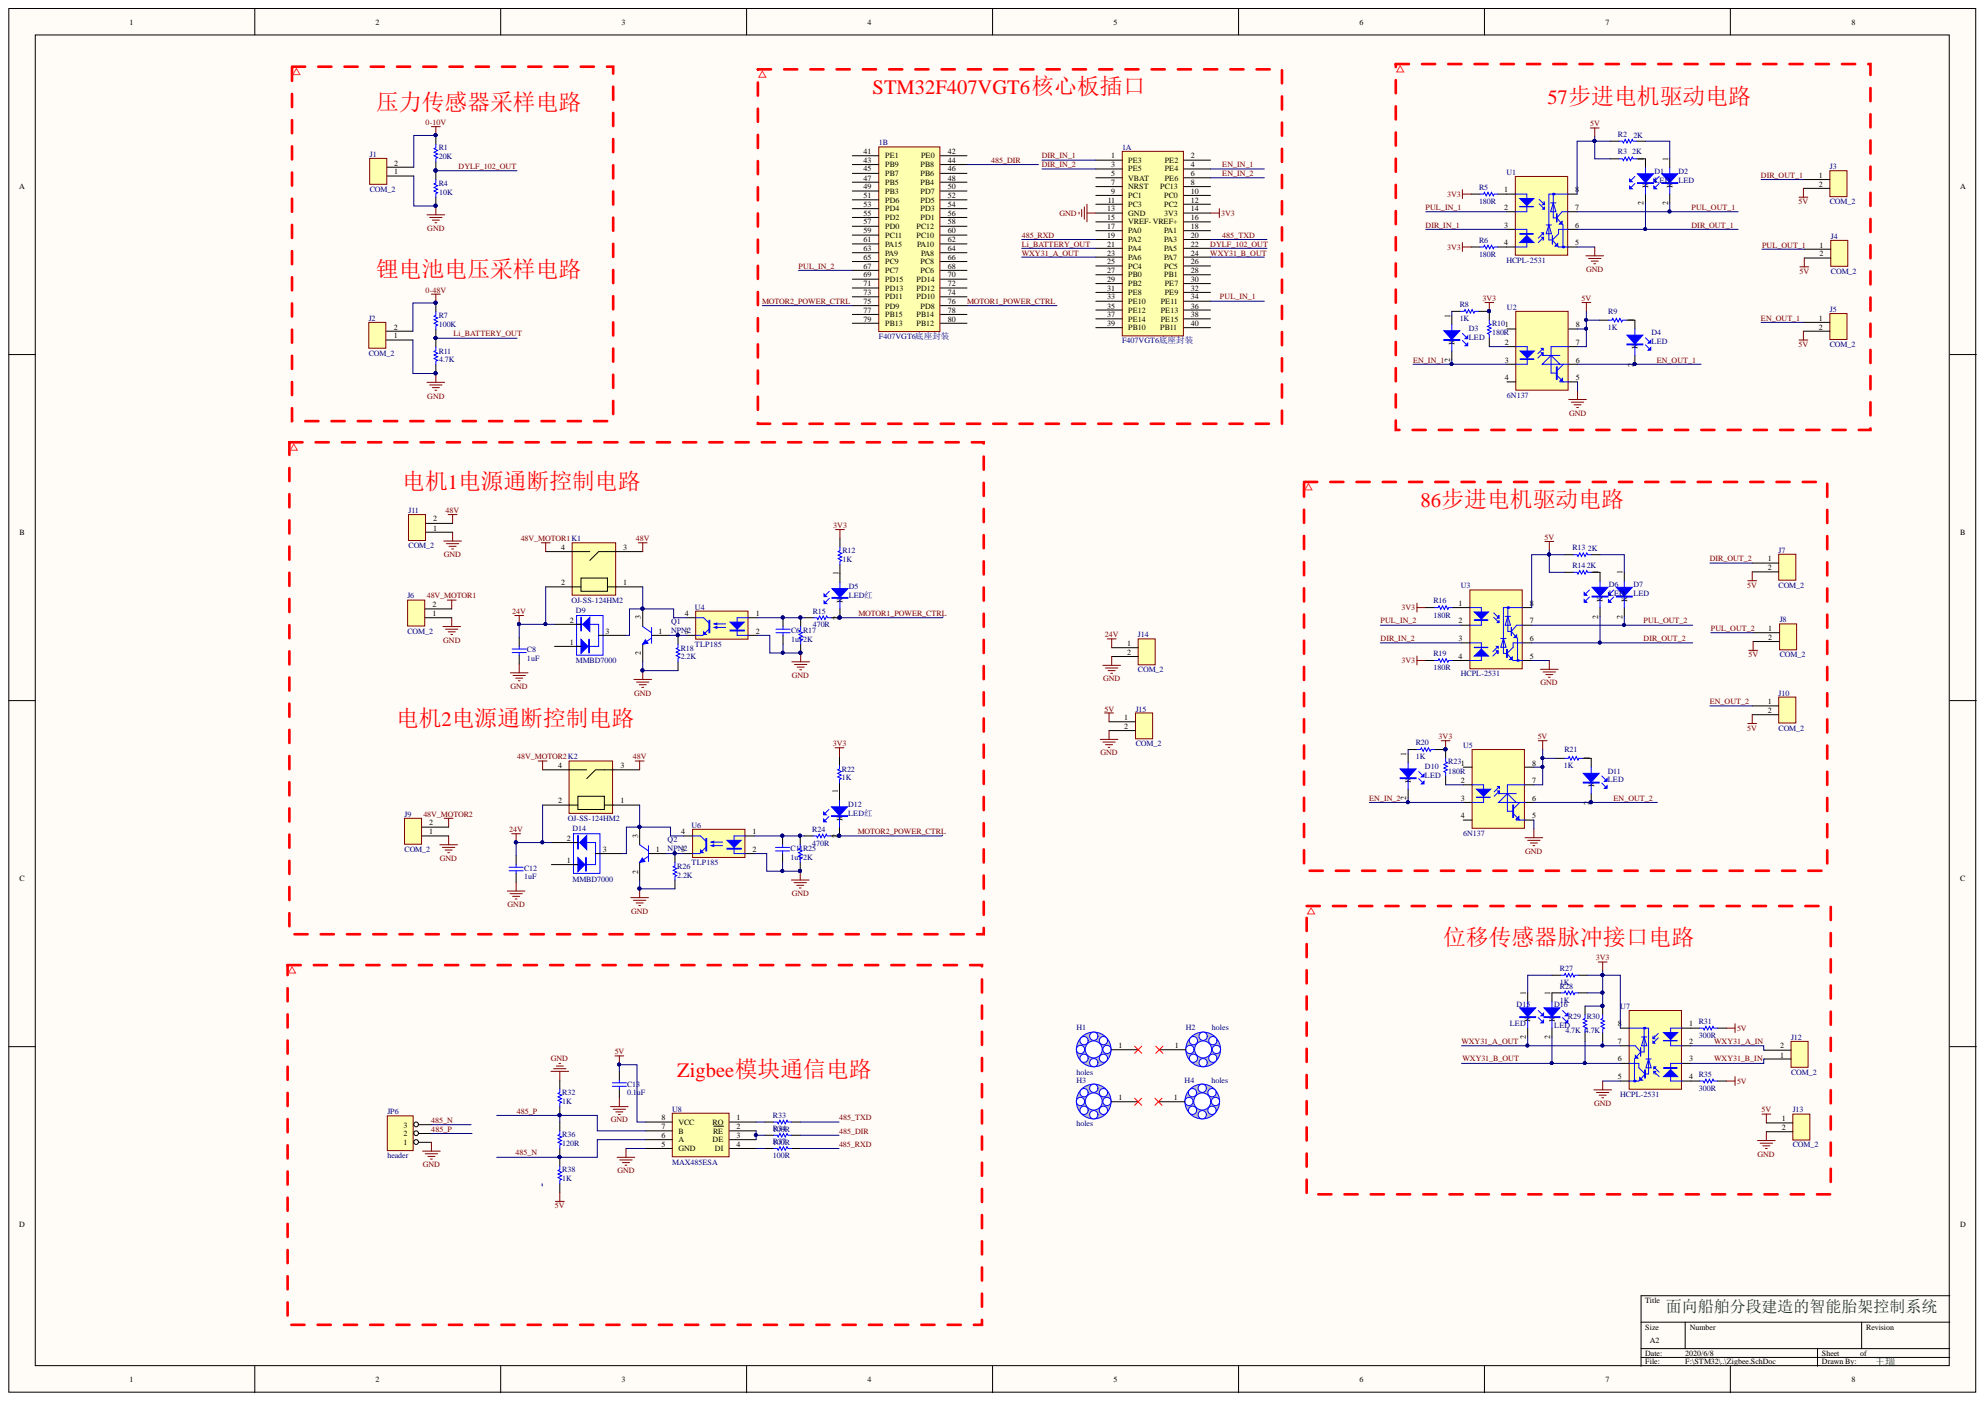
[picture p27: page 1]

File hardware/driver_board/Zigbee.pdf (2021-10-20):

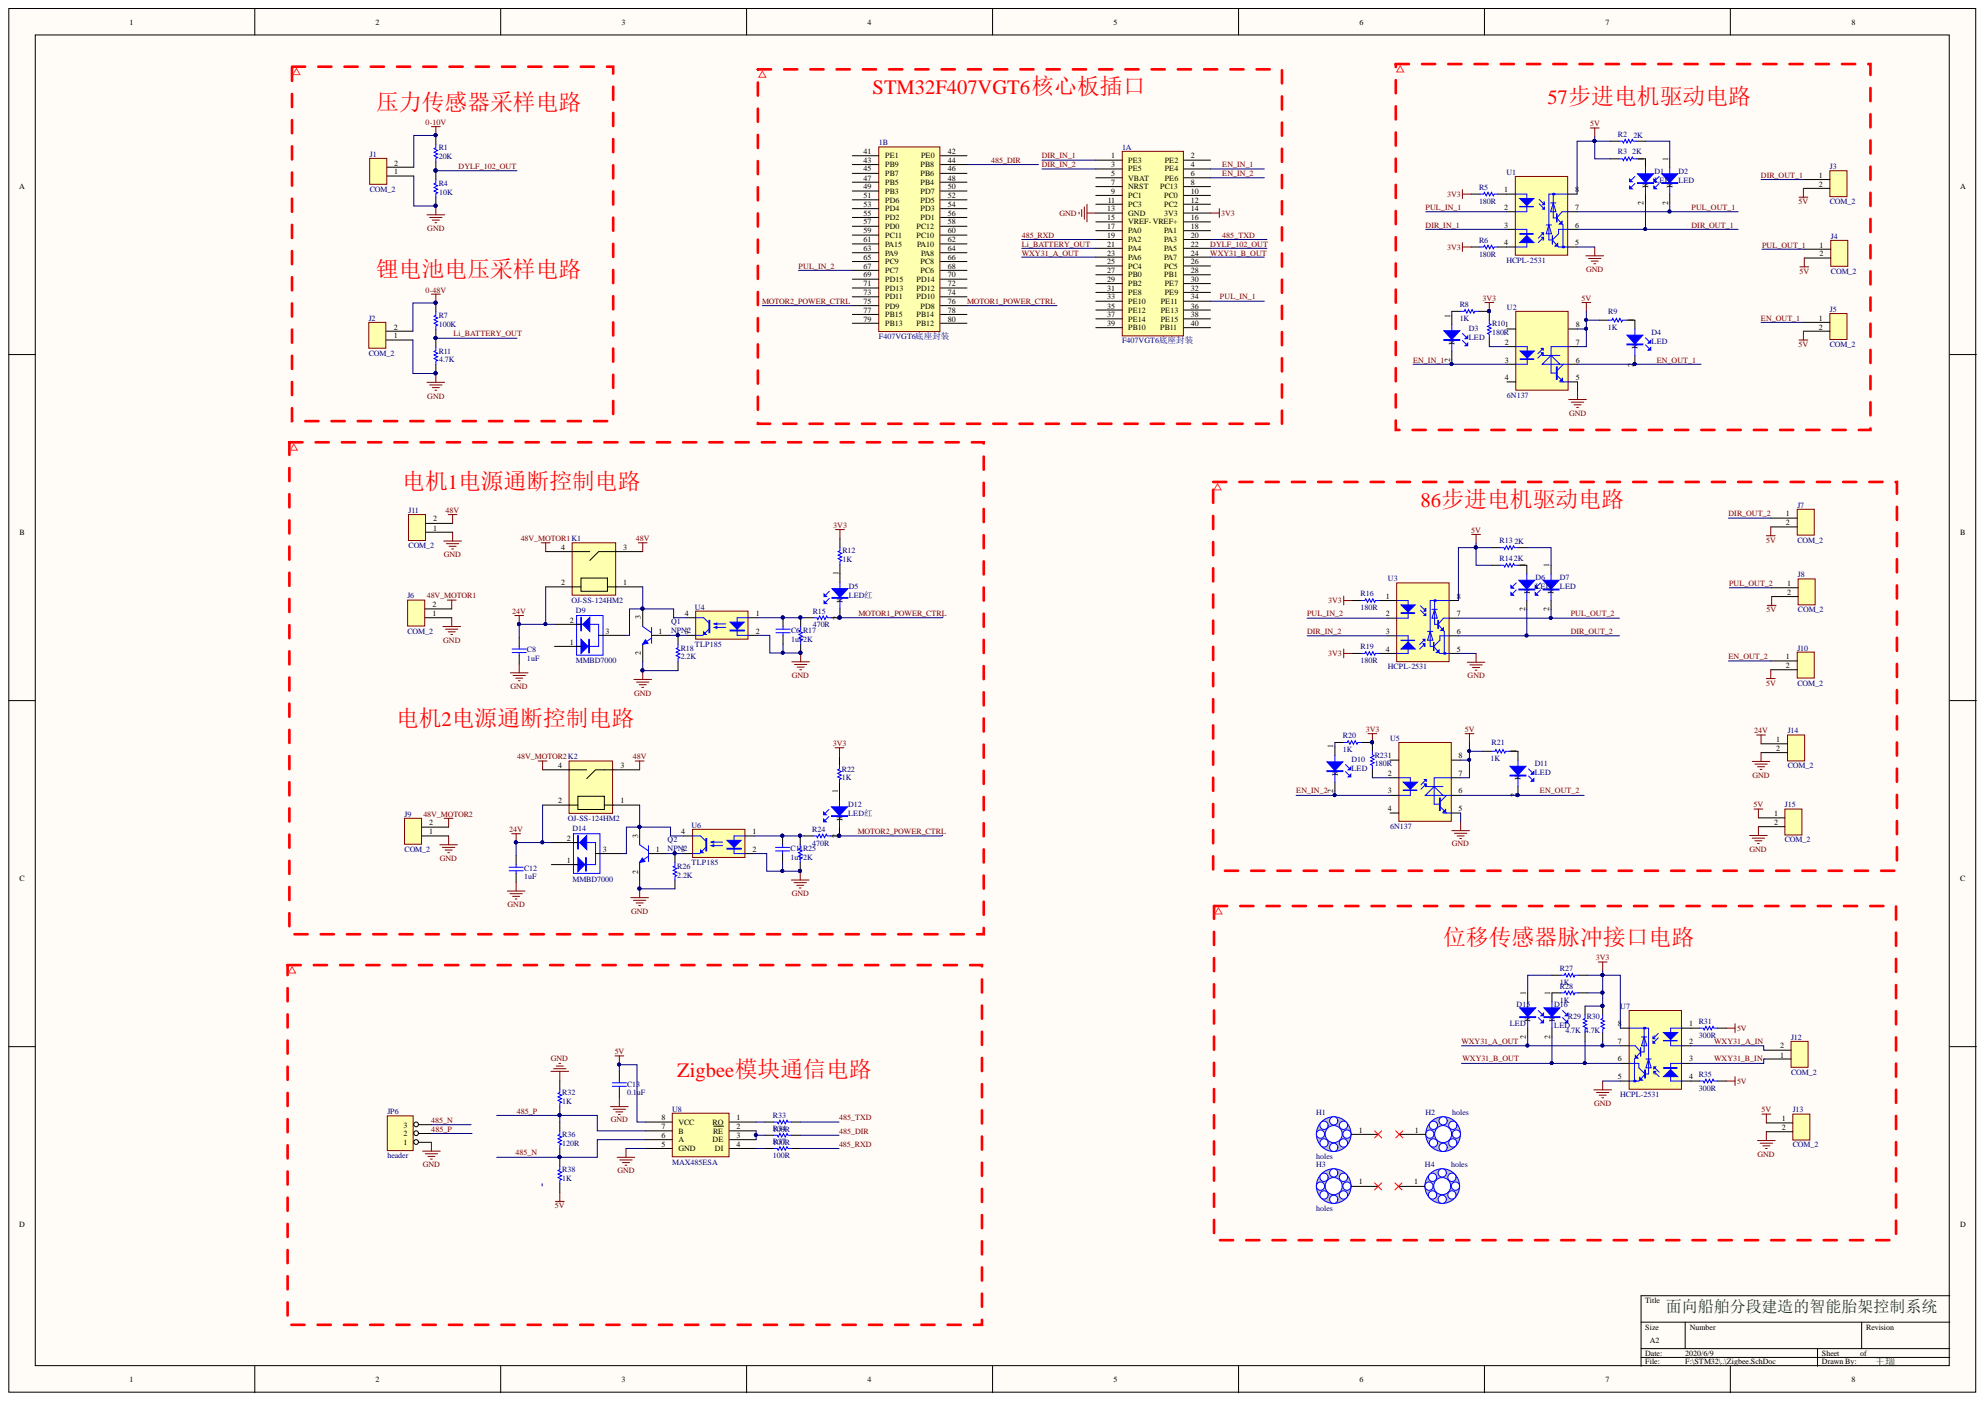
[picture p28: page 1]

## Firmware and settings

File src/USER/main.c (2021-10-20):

#include "stm32f4xx.h"
#include "usart.h"
#include "delay.h"
#include "led.h"
#include "motor1.h"
#include "motor2.h"
#include "height.h"
#include "adc.h"
#include "rs485.h"
#include "includes.h"
#include "math.h"
//毕业设计-智能胎架控制系统程序
//MCU：STM32F407VGT6
//修改日期:2020/05/20
//版本：V2.0

/////////////////////////UCOSII任务设置///////////////////////////////////
//START 任务
//设置任务优先级
#define START_TASK_PRIO      			10 //开始任务的优先级设置为最低
//设置任务堆栈大小
#define START_STK_SIZE  				64
//任务堆栈	
OS_STK START_TASK_STK[START_STK_SIZE];
//任务函数
void start_task(void *pdata);	

//底盘前进任务
//设置任务优先级
#define FORWARD_TASK_PRIO       			9 
//设置任务堆栈大小
#define FORWARD_STK_SIZE  					128
//任务堆栈	
OS_STK FORWARD_TASK_STK[FORWARD_STK_SIZE];
//任务函数
void forward_task(void *pdata);

//底盘后退任务
//设置任务优先级
#define BACK_TASK_PRIO       			8 
//设置任务堆栈大小
#define BACK_STK_SIZE  					128
//任务堆栈	
OS_STK BACK_TASK_STK[BACK_STK_SIZE];
//任务函数
void back_task(void *pdata);

//丝杠上升任务
//设置任务优先级
#define UP_TASK_PRIO       			7 
//设置任务堆栈大小
#define UP_STK_SIZE  					128
//任务堆栈	
OS_STK UP_TASK_STK[UP_STK_SIZE];
//任务函数
void up_task(void *pdata);

//丝杠下降任务
//设置任务优先级
#define DOWN_TASK_PRIO       			6 
//设置任务堆栈大小
#define DOWN_STK_SIZE  					128
//任务堆栈	
OS_STK DOWN_TASK_STK[DOWN_STK_SIZE];
//任务函数
void down_task(void *pdata);

//丝杠位置控制任务
//设置任务优先级
#define POSITION_TASK_PRIO       			5 
//设置任务堆栈大小
#define POSITION_STK_SIZE  					128
//任务堆栈	
OS_STK POSITION_TASK_STK[POSITION_STK_SIZE];
//任务函数
void position_task(void *pdata);

//压力检测任务
//设置任务优先级
#define PRESSURE_TASK_PRIO       			4 
//设置任务堆栈大小
#define PRESSURE_STK_SIZE  					128
//任务堆栈	
OS_STK PRESSURE_TASK_STK[PRESSURE_STK_SIZE];
//任务函数
void pressure_task(void *pdata);

//位移检测任务
//设置任务优先级
#define HEIGHT_TASK_PRIO       			    3
//设置任务堆栈大小
#define HEIGHT_STK_SIZE  					128
//任务堆栈	
OS_STK HEIGHT_TASK_STK[HEIGHT_STK_SIZE];
//任务函数
void height_task(void *pdata);

//主任务
//设置任务优先级
#define MAIN_TASK_PRIO       			2 
//设置任务堆栈大小
#define MAIN_STK_SIZE  		    	128
//任务堆栈	
OS_STK MAIN_TASK_STK[MAIN_STK_SIZE];
//任务函数
void main_task(void *pdata);

//串口通信任务
//设置任务优先级
#define USART_TASK_PRIO       			1 
//设置任务堆栈大小
#define USART_STK_SIZE  		    	128
//任务堆栈	
OS_STK USART_TASK_STK[USART_STK_SIZE];
//任务函数
void usart_task(void *pdata);

//////////////////////////////////////////////////////////////////////////////
OS_EVENT * sem_position;		//信号量指针
OS_EVENT * sem_forward;			//信号量指针
OS_EVENT * sem_back;			//信号量指针
OS_EVENT * msg_command;		    //指令信号量指针
OS_EVENT * Mbox_height;          //高度检测消息邮箱

OS_EVENT * q_msg_adc;			//ADC消息队列

OS_EVENT * q_msg_up;			    //丝杠上升消息队列
OS_EVENT * q_msg_down;			//丝杠下降消息队列
OS_EVENT * q_msg_forward;			//底盘前进消息队列
OS_EVENT * q_msg_back;			//底盘后退消息队列

void * MsgGrp_ADC[4];			//adc消息队列存储地址,最大支持4个消息
void * MsgGrp_up[2];			//adc消息队列存储地址,最大支持4个消息
void * MsgGrp_down[2];			//adc消息队列存储地址,最大支持4个消息
void * MsgGrp_forward[2];		//adc消息队列存储地址,最大支持4个消息
void * MsgGrp_back[2];			//adc消息队列存储地址,最大支持4个消息
//创建消息队列，首先需要定义一个指针数组(用于存放消息邮箱)，然后把各个消息数据缓冲区的首地址存入这个数组中

//系统初始化
void system_init(void)
{
    uart_init(115200);            //初始化串口波特率为115200
	delay_init(168);              //延时初始化
	RS485_Init(38400);
	Encoder_Timer3_Init();
	LED_Init();		        //初始化LED端口---调试用
	TIM1_OPM_RCR_Init(999,168-1); //初始化TIM1为1MHz的计数频率  单脉冲+重复计数模式
    TIM8_OPM_RCR_Init(999,168-1); //初始化TIM8为1MHz的计数频率  单脉冲+重复计数模式
	Driver1_Init();
	Driver_Init();
	Adc_Init(); 				//ADC通道初始化

}

/*****************主函数********************/
int main(void)
{
	NVIC_PriorityGroupConfig(NVIC_PriorityGroup_2);//设置系统中断优先级分组2
	
	system_init();//系统初始化
	
	OSInit();//初始化UCOSII
	OSTaskCreate(start_task,(void *)0,(OS_STK *)&START_TASK_STK[START_STK_SIZE-1],START_TASK_PRIO );//创建起始任务
    OSStart();
}
//开始任务
void start_task(void *pdata)
{
	OS_CPU_SR cpu_sr=0;
	pdata = pdata; 	
	
	q_msg_adc=OSQCreate(&MsgGrp_ADC[0],4);	//创建adc处理任务消息队列
	q_msg_up=OSQCreate(&MsgGrp_up[0],2);	//创建
	q_msg_down=OSQCreate(&MsgGrp_down[0],2);	//创建a
	q_msg_forward=OSQCreate(&MsgGrp_forward[0],2);	//创建
	q_msg_back=OSQCreate(&MsgGrp_back[0],2);	//创建
	
	Mbox_height=OSMboxCreate((void *)0); //建立高度检测消息邮箱
	
	msg_command=OSMboxCreate((void*)0);	//创建消息邮箱
	sem_position=OSSemCreate(0);		//创建信号量
	sem_forward=OSSemCreate(0);		//创建信号量
	sem_back=OSSemCreate(0);		//创建信号量
	
	OSStatInit();		//初始化统计任务.这里会延时1秒钟左右
	
	OS_ENTER_CRITICAL();			//进入临界区(无法被中断打断) 
	OSTaskCreate(forward_task,(void *)0,(OS_STK*)&FORWARD_TASK_STK[FORWARD_STK_SIZE-1],FORWARD_TASK_PRIO);
	OSTaskCreate(back_task,(void *)0,(OS_STK*)&BACK_TASK_STK[BACK_STK_SIZE-1],BACK_TASK_PRIO);
	OSTaskCreate(up_task,(void *)0,(OS_STK*)&UP_TASK_STK[UP_STK_SIZE-1],UP_TASK_PRIO);
	OSTaskCreate(down_task,(void *)0,(OS_STK*)&DOWN_TASK_STK[DOWN_STK_SIZE-1],DOWN_TASK_PRIO);
	OSTaskCreate(position_task,(void *)0,(OS_STK*)&POSITION_TASK_STK[POSITION_STK_SIZE-1],POSITION_TASK_PRIO);
	OSTaskCreate(pressure_task,(void *)0,(OS_STK*)&PRESSURE_TASK_STK[PRESSURE_STK_SIZE-1],PRESSURE_TASK_PRIO);
	OSTaskCreate(height_task,(void *)0,(OS_STK*)&HEIGHT_TASK_STK[HEIGHT_STK_SIZE-1],HEIGHT_TASK_PRIO);
	OSTaskCreate(main_task,(void *)0,(OS_STK*)&MAIN_TASK_STK[MAIN_STK_SIZE-1],MAIN_TASK_PRIO);
	OSTaskCreate(usart_task,(void *)0,(OS_STK*)&USART_TASK_STK[USART_STK_SIZE-1],USART_TASK_PRIO);
    
	OSTaskSuspend(START_TASK_PRIO);	//挂起起始任务
	OS_EXIT_CRITICAL();	//退出临界区(可以被中断打断)
	
}
//底盘前进任务
void forward_task(void *pdata)
{
    int steps;
    int speed;	
	int acceleration = 1;//默认加速度 
    int deceleration = 1;//默认减速度

	int *msg_forward;
    u8 err;
	
	while(1)
	{
		msg_forward=OSQPend(q_msg_forward,0,&err);//等待接收邮箱信息(指针msg指向buffer)
		steps=*msg_forward;
		speed=*(msg_forward+1);
		GPIO_SetBits(GPIOE,GPIO_Pin_5); //PE5输出高 顺时针方向  DRIVER2_DIR
        MSD_Move(steps, acceleration, deceleration, speed);
		
		LED1=!LED1;
		delay_ms(100);
	}
}	
//底盘后退任务
void back_task(void *pdata)
{
	int steps;
    int speed;	
	int acceleration = 1;//默认加速度 
    int deceleration = 1;//默认减速度

	int *msg_back;
	
	u8 err;
	while(1)
	{
		msg_back=OSQPend(q_msg_back,0,&err);//等待接收邮箱信息(指针msg指向buffer)
        steps=-(*msg_back);
		speed=*(msg_back+1);
	    MSD_Move(steps, acceleration, deceleration, speed);
		
		LED1=!LED1;
		delay_ms(10);
	}
}
//丝杠上升任务
void up_task(void *pdata)
{
	int steps;	
	int speed;
	int acceleration = 1;//默认加速度 
    int deceleration = 1;//默认减速度
	
	int *msg_up;
    u8 rs485[3];
	
	u8 err;
	rs485[0]=6;
	rs485[1]=6;
	rs485[2]=6;
	
	
	while(1)
	{
		msg_up=OSQPend(q_msg_up,0,&err);//等待接收邮箱信息(指针msg指向buffer)
		steps=*msg_up;
		speed=*(msg_up+1);
		
		MSD_Move1(steps, acceleration, deceleration, speed);
		//rs485[1]=speed/255;
		//rs485[2]=speed%255;
		//RS485_Send_Data(rs485,3);
		LED1=!LED1;
		delay_ms(10);
	}
}
//丝杠下降任务
void down_task(void *pdata)
{		
	int steps;	
	int speed;
	int acceleration = 1;//默认加速度 
    int deceleration = 1;//默认减速度
  
	int *msg_down;
	
	u8 err;
	while(1)
	{
		msg_down=OSQPend(q_msg_down,0,&err);//等待接收邮箱信息(指针msg指向buffer)
		steps=-(*msg_down);
		speed=*(msg_down+1);
		MSD_Move1(steps, acceleration, deceleration, speed);
		
		LED1=!LED1;
		delay_ms(10);
	}
	
}
	
//丝杠位置控制任务、用于扩展为丝杠运动闭环控制时使用
void position_task(void *pdata)
{
	//u8 err;
	while(1)
	{
		//OSSemPend(sem_position,0,&err);  
		delay_ms(10);
	}
}
//ADC检测任务---获取压力值、锂电池电压值
void pressure_task(void *pdata)
{
	u16 adc1;  //压力adc值
	u16 adc2;  //锂电池电压adc值
	float temp1;//压力--小数
	float temp2;//锂电池电压--小数
	u8 temp1_int;//压力--整数
	u8 temp2_int;//锂电池电压--整数
	u8 temp1_float;//压力--小数部分*100
	u8 temp2_float;//锂电池电压--小数部分*100
	u8 adc[4];
	while(1)
	{
		adc1=Get_Adc1(ADC_Channel_5); 
		adc2=Get_Adc2(ADC_Channel_4);
		//adc[4]=adc1;
		//printf("%d\r\n",adc1);
		//printf("%d\r\n",adc2);
		//adc1=Get_Adc1_Average(ADC_Channel_5,20);//获取通道5的转换值，20次取平均
		//adc2=Get_Adc2_Average(ADC_Channel_4,20);//获取通道4的转换值，20次取平均
		
		temp1=(float)15*3*adc1*(3.3/4095); //获取计算后的带小数的实际压力值--小数
		
		temp2=(float)(104.7/4.7)*adc2*(3.3/4095);   //获取计算后的带小数的实际锂电池电压值--小数

		temp1_int=temp1; //赋值压力整数部分
		temp2_int=temp2; //赋值锂电池电压整数部分
		
		temp1-=temp1_int; //整数部分去掉，留下小数部分，比如3.1111-3=0.1111
		temp2-=temp2_int; //整数部分去掉
	
		temp1*=100; //小数部分乘以100  如上述temp1=11.11		
		temp2*=100; //小数部分乘以100
		
		temp1_float=temp1;//相当于保留两位小数。
		temp2_float=temp2;//相当于保留两位小数。
		
		adc[0]=temp1_int;
		adc[1]=temp1_float;
		adc[2]=temp2_int;
		adc[3]=temp2_float;
		
		
		OSQPost(q_msg_adc,&adc[0]); //发送到队列
		//OSQPost(q_msg_adc,(void*)&temp1_float); //发送到队列
		//OSQPost(q_msg_adc,(void*)&temp2_int); //发送到队列
		//OSQPost(q_msg_adc,(void*)&temp2_float); //发送到队列
		delay_ms(10);
	}
}
//位移检测任务
void height_task(void *pdata)
{
	int height_pulse;
	while(1)
	{
		height_pulse = read_encoder()/4;
		//height_pulse = 256;
		OSMboxPost(Mbox_height,&height_pulse);//通过邮箱发送高度脉冲信息(指针)给485通信任务
		
		//LED0=!LED0;
		//LED1=!LED1;
		delay_ms(10);
	}
}

void main_task(void *pdata)
{
	//u8 i=0;
    //u8 key;
	u8 *msg_adc;
	u16 *msg_height;
	
	u8 pressure_int;//压力--整数
	u8 li_int;//锂电池电压--整数
	u8 pressure_float;//压力--小数部分*100
	u8 li_float;//锂电池电压--小数部分*100
	u16 height;//高度脉冲
	u8 height_H;//高度脉冲高8位
	u8 height_L;//高度脉冲低8位
	//u16 adc1;
	u8 err1;
	u8 err2;
	u8 rs485_tx_buf[]={237, 06, 87, 32, 0, 0, 0, 0, 0, 0};//这里先假设发送的数据为6位；接收缓冲的数据来源于压力、位移采集模块的处理结果；
	u8 command;
	//rs485[0]=1;
	while(1)
	{
		
		msg_adc=OSQPend(q_msg_adc,0,&err1);//等待接收邮箱信息(指针msg指向buffer)
		pressure_int=*msg_adc;
		pressure_float=*(msg_adc+1);
		li_int=*(msg_adc+2);
		li_float=*(msg_adc+3); 
		//adc1=*(msg_adc+4);		
		
		msg_height=OSMboxPend(Mbox_height,0,&err2);//等待接收邮箱信息(指针msg_height指向位移检测任务中的height_pulse) 
		height=*msg_height;
		height_H = height / 255;
		height_L = height % 255;
		
		rs485_tx_buf[4] = pressure_int;
		rs485_tx_buf[5] = pressure_float;
		rs485_tx_buf[6] = li_int;
		rs485_tx_buf[7] = li_float;
		rs485_tx_buf[8] = height_H;
		rs485_tx_buf[9] = height_L;
		RS485_Send_Data(rs485_tx_buf,10);
		delay_ms(2000);
		
	}	
        
}
	
//485通信任务（Zigbee）
void usart_task(void *pdata)
{
	u8 key;
	u8 err1=0x00;
	u8 ture=0x01;
	u8 err2=0x03;
	u8 rs485_rx_buf[13];
	u8 rs[1];
	int up[2];
	int down[2];
	int forward[2];
	int back[2];
	
	rs[0]=6;
	while(1)
	{
	   key=0;
	   //RS485_Send_Data(&key,1);
		delay_ms(1000);
       //GPIO_ResetBits(GPIOB,GPIO_Pin_8);		
	   RS485_Receive_Data(rs485_rx_buf,&key);
	   if(key!=0)//接收到有数据
	   {
		   if(key!=13)
			   RS485_Send_Data(&err1,1);//数据长度错误，返回0x00
		   
		   else 
		   {
		   if(rs485_rx_buf[0]==0xED&&rs485_rx_buf[1]==0x07&&rs485_rx_buf[2]==0x57&&rs485_rx_buf[3]==0x21&&rs485_rx_buf[11]==0x57&&rs485_rx_buf[12]==0x20)//数据格式正确、执行相应命令
		   {
			   RS485_Send_Data(&ture,1);//数据格式正确，返回0x01，并提取数据位
			   switch(rs485_rx_buf[4])  //指令选择位
		     {
			
			    case 1://控制丝杠位置  上升  距离  速度 
                
 				    up[0]=(int)(3553.57*(255*rs485_rx_buf[5] + rs485_rx_buf[6]));
				    up[1]=(int)(3553.57*rs485_rx_buf[7]);
				
				    OSQPost(q_msg_up,&up[0]); //发送到队列
	
				    //RS485_Send_Data(rs485,1);
			        delay_ms(20);
				    
			        break;
			    case 2://控制底盘位置  下降  距离  速度
					down[0]=(int)(3553.57*(255*rs485_rx_buf[5] + rs485_rx_buf[6]));
				    down[1]=(int)(3553.57*rs485_rx_buf[7]);
							
				    OSQPost(q_msg_down,&down[0]); //发送到队列
				    //MSD_Move(steps, acceleration, deceleration, speed);
			        delay_ms(20);
			       
				    break;
			    case 3://控制底盘位置  前进 距离  速度
					forward[0]=abs((int)(1527.88*(255*rs485_rx_buf[8] + rs485_rx_buf[9])));
				    forward[1]=(int)(1527.88*rs485_rx_buf[10]);
						
					OSQPost(q_msg_forward,&forward[0]); //发送到队列
				    
				    break;
				case 4://控制底盘位置  后退  距离  速度
					back[0]=(int)(1527.88*(255*rs485_rx_buf[8] + rs485_rx_buf[9]));
				    back[1]=(int)(1527.88*rs485_rx_buf[10]);
				
					OSQPost(q_msg_back,&back[0]); //发送到队列
				    
				    break;
				case 5://丝杠停止 
					TIM_Cmd(TIM1, DISABLE);
					TIM_SetCounter(TIM1,0);//计数器清零
					
				    break;
				case 6://底盘停止
					TIM_Cmd(TIM8, DISABLE);
				    TIM_SetCounter(TIM8,0);//计数器清零
				
				    break;
		     }	
			     //key = 0;
			   LED0=!LED0;//
		   }
		   else
		     RS485_Send_Data(&err2,1);//报头or报尾错误，返回0x03
		   
	       } 
	   }  
	   
	   key=0;
	   delay_ms(100);   
	}

}

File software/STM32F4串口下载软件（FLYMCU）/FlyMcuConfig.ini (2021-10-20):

[Comm]
Port=-1
PortBps=5
[FileSetting]
chkbReloadFile=1
FileName=F:\STM32\Control Program\OBJ\Template.hex
PageControl1Index=1
N2Checked=1
language=0
[LPCSetting]
LastSuccessBps=76800
OscFreq=20000
rgLpcEraseAllBlock=1
rgLpc1FC=0
cbISPEN_WDT=0
[STMSetting]
cbSTMExecAfterFlash=1
cbVerify=1
cbRtsDtrUsage->ItemIndex=3
MenuUseEagleComm=0
menuBeepEnable=0
menuEnableHighBps=0
menuUseRamIsp=0
cbAutoProgram=0
cbSTMWriteOption=0
STMOptionBytes=A5FFFFFFFFFFFFFF
STM32F2_F4OptionBytes=AAFFFFF
[FormWindow]
WindowState=0
WindowXDPI=96
WindowYDPI=96
WindowClientHeight96=371
WindowClientWidth96=638
WindowLeft96=511
WindowTop96=233
[fmSerialNoSetting]
cbUseID=0
medAddress=0x08000000
medLength=16
medInit=4
medIncLen=1
rgEndian=0
rgSnInFlashOrEeprom=0
cbSerialNoFormat=0
[fmSerialization]
cbEnableSerialization=0
edMcuIspDllFileName=
[fmProgCount]
medProgCount=0
[fmMSP430Settings]
orgVecs=FFFFFFFFFFFFFFFFFFFFFFFFFFFFFFFFFFFFFFFFFFFFFFFFFFFFFFFFFFFFFFFF
Vecs=FFFFFFFFFFFFFFFFFFFFFFFFFFFFFFFFFFFFFFFFFFFFFFFFFFFFFFFFFFFFFFFFFFFFFFFFFFFFFFFFFFFFFFFFFFFFFFFFFFFFFFFFFFFFFFFFFFFFFFFFFFFFFFFF
BSLKeys=FFFFFFFFFFFFFFFFFFFFFFFFFFFFFFFFFFFFFFFFFFFFFFFFFFFFFFFFFFFFFFFFFFFFFFFFFFFFFFFFFFFFFFFFFFFFFFFFFFFFFFFFFFFFFFFFFFFFFFFFFFFFFFFFFFFFFFFFFFFFFFFFFFFFFFFFFFFFFFFFFFFFFFFFFFFFFFFFFFFFFFFFFFFFFFFF
PortSettings=1
MiscSettings=0
cbEnableAdvanceVectorModify=0

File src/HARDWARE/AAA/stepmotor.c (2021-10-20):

#include "stepmotor.h"
#if STEP_MOTOR

StepMotorAddSpeed MotorAddSpeed;




/*******************************************************************************
*							定时器4初始化函数
*
*函数名：void TIM5_Int_Init(u16 arr,u16 psc)
*
*形参：	arr 		预装载值
		psc			分频系数
*
*返回值：	无
*
*
*******************************************************************************/
void TIM4_Int_Init(u16 arr,u16 psc)
{
	GPIO_InitTypeDef GPIO_InitStructure;
	TIM_TimeBaseInitTypeDef  TIM_TimeBaseStructure;
	TIM_OCInitTypeDef  TIM_OCInitStructure;
	
 
	RCC_APB1PeriphClockCmd(RCC_APB1Periph_TIM4, ENABLE);	//使能定时器3时钟
 	RCC_APB2PeriphClockCmd(RCC_APB2Periph_GPIOB  | RCC_APB2Periph_AFIO, ENABLE);  //使能GPIO外设和AFIO复用功能模块时钟 
 
   //设置该引脚为复用输出功能,输出TIM4 CH3的PWM脉冲波形	GPIOB.8
	GPIO_InitStructure.GPIO_Pin = GPIO_Pin_8; 			//TIM_CH2
	GPIO_InitStructure.GPIO_Mode = GPIO_Mode_AF_PP;  	//复用推挽输出
	GPIO_InitStructure.GPIO_Speed = GPIO_Speed_50MHz;
	GPIO_Init(GPIOB, &GPIO_InitStructure);				//初始化GPIO
 
   //初始化TIM4
	TIM_TimeBaseStructure.TIM_Period = arr; 						//设置在下一个更新事件装入活动的自动重装载寄存器周期的值
	TIM_TimeBaseStructure.TIM_Prescaler =psc; 						//设置用来作为TIMx时钟频率除数的预分频值 
	TIM_TimeBaseStructure.TIM_ClockDivision = 0; 					//设置时钟分割:TDTS = Tck_tim
	TIM_TimeBaseStructure.TIM_CounterMode = TIM_CounterMode_Up;  	//TIM向上计数模式
	TIM_TimeBaseInit(TIM4, &TIM_TimeBaseStructure); 				//根据TIM_TimeBaseInitStruct中指定的参数初始化TIMx的时间基数单位
	
	//初始化TIM3 Channel2 PWM模式	 
	TIM_OCInitStructure.TIM_OCMode = TIM_OCMode_PWM1; 				//选择定时器模式:TIM脉冲宽度调制模式2
 	TIM_OCInitStructure.TIM_OutputState = TIM_OutputState_Enable; 	//比较输出使能
	TIM_OCInitStructure.TIM_OCPolarity = TIM_OCPolarity_High; 		//输出极性:TIM输出比较极性高
	TIM_OC3Init(TIM4, &TIM_OCInitStructure);  						//根据T指定的参数初始化外设TIM3 OC2
 
	TIM_OC3PreloadConfig(TIM4, TIM_OCPreload_Enable); 				 //使能TIM3在CCR2上的预装载寄存器
 
//	TIM_Cmd(TIM4, ENABLE);  //使能TIM4
}

u32 PluseNum = 0;

/*******************************************************************************
*							步进电机初始化
*
*函数名：void MotorInit(void)
*
*形参：	无
*
*返回值：	无
*
*
*******************************************************************************/
void MotorInit(void)
{
	GPIO_InitTypeDef  GPIO_InitStructure;

	RCC_APB2PeriphClockCmd(RCC_APB2Periph_GPIOE|RCC_APB2Periph_GPIOB|RCC_APB2Periph_GPIOD, ENABLE);	 

	GPIO_InitStructure.GPIO_Pin = GPIO_Pin_14|GPIO_Pin_15;				
	GPIO_InitStructure.GPIO_Mode = GPIO_Mode_Out_PP;  //推挽输出
	GPIO_InitStructure.GPIO_Speed = GPIO_Speed_50MHz; 
	GPIO_Init(GPIOE, &GPIO_InitStructure);	
	GPIO_ResetBits(GPIOE,GPIO_Pin_14|GPIO_Pin_15);
	
	GPIO_InitStructure.GPIO_Pin = GPIO_Pin_10|GPIO_Pin_11;				
	GPIO_InitStructure.GPIO_Mode = GPIO_Mode_Out_PP;  //推挽输出
	GPIO_InitStructure.GPIO_Speed = GPIO_Speed_50MHz; 
	GPIO_Init(GPIOB, &GPIO_InitStructure);	
	GPIO_SetBits(GPIOB,GPIO_Pin_11);
	GPIO_ResetBits(GPIOB,GPIO_Pin_10);	

	MF = 0;
	DIR = 1;
	DE = 0;
	
	TIM3_Int_Init(1000-1);	//计算PWM波的脉冲来进入中断
	TIM4_Int_Init(1000,71);	//1Mhz.1ms一个10us的脉冲 步进电机的脉冲必须大于2.5us
	TIM_SetCompare3(TIM4,10);
	delay_ms(10);
}

/*******************************************************************************
*							步进电机运行
*
*函数名：void MotorStart(u8 UpORDown,u8 speed,u16 tim3_cnt_int)
*
*形参：	UpORDown	升降台运行方向
		speed		升降台运行速度 1000即1ms一个脉冲 脉冲越快电机运行越快
		tim3_cnt_int	TIM3写入的溢出值
*
*返回值：	无
*
*
*******************************************************************************/
void MotorStart(u8 UpORDown,u16 speed,u16 tim3_cnt_int)
{
	TIM4->ARR = speed-1;
	TIM3->ARR = tim3_cnt_int-1;
	
	MF = 1;	//电机使能信号
	DR = UpORDown;		//电机方向

	TIM_Cmd(TIM3, ENABLE);
	TIM_Cmd(TIM4, ENABLE); 
}



/*******************************************************************************
*							步进电机停止
*
*函数名：void MotorStart(u8 UpORDown,u8 speed)
*
*形参：	void
*
*返回值：void
*
*
*******************************************************************************/
void MotorStop(void)
{	
	TIM_Cmd(TIM4, DISABLE); 
	TIM_Cmd(TIM3, DISABLE); 	
//	MF = 0;
//	DR = 1;	
}

/*******************************************************************************
*							步进电机运行给定脉冲
*
*函数名：void MotorStartPluse(u32 pluse,u8 UpORDown)
*
*形参：	pluse		脉冲数
		UpORDown	升降台方向
*
*返回值：void
*
*描述：	步进电机匀加速时间和加速次数，起始频率和目标频率可以再宏定义中的修改
*
*
*******************************************************************************/
void MotorStartPluse(u32 pluse,u8 UpORDown)
{
	u16 add_pluse = 0;
	u16	Next_F = 0;
	u8 a = 1;
	delay_ms(10);
	MotorAddSpeed.pluse_send = 0;
	
	if(UpORDown==UP)
	{
		MotorAddSpeed.flag				|=	1<<1;
		MotorAddSpeed.flag				&=	 ~(1<<7);
		MotorAddSpeed.pluse_ObjSend 	= 	pluse;
	}
	else if(UpORDown==DOWN && (MotorAddSpeed.flag & (1<<7))!=1)
	{
		MotorAddSpeed.flag				&=	~(1<<1);
		MotorAddSpeed.pluse_ObjSend 	=	pluse;	
	}
	else if(UpORDown==DOWN && (MotorAddSpeed.flag & (1<<7))==1)	return;//在最低位置不能下降

	if(pluse>=NEED_PLUSE)												//适合匀加速运动
	{
		MotorAddSpeed.Arr_tim4_start	=	TIMER_F/START_F;
		MotorAddSpeed.Add_Cnt			=	0;
		MotorAddSpeed.Add_Minus			=	ADD;
		MotorAddSpeed.Arr_tim3			=	2;
		Next_F 		 =	START_F+(MotorAddSpeed.Add_Cnt*ADD_SPEED);
		add_pluse = T_ADD*Next_F/1000;

		MotorStart(UpORDown,MotorAddSpeed.Arr_tim4_start,MotorAddSpeed.Arr_tim3);
		while(1)
		{
			if( MotorAddSpeed.pluse_send >= pluse-(NEED_PLUSE/2) && a==1)
			{
				a=0;
				MotorAddSpeed.Add_Minus			=	MINUS;
				add_pluse = MotorAddSpeed.pluse_send;
			}
			
			if(MotorAddSpeed.pluse_send>=add_pluse && Next_F<OBJ_F && \
				MotorAddSpeed.Add_Minus==ADD)								//达到加速条件 在加速阶段											
			{
//				u2_printf("1111111\t%d\r\n",MotorAddSpeed.pluse_send);//调试串口输出
				MotorAddSpeed.Add_Cnt++;
				Next_F 		 =	START_F+(MotorAddSpeed.Add_Cnt*ADD_SPEED);
				MotorAddSpeed.Arr_tim4_start	=	TIMER_F/Next_F;
				add_pluse 	+= T_ADD*Next_F/1000;							//计算出下次需要加速时的累计脉冲值
				TIM4->ARR	 = MotorAddSpeed.Arr_tim4_start-1;	
			}
			
			else if(MotorAddSpeed.pluse_send >= pluse-(NEED_PLUSE/2) && Next_F>START_F && MotorAddSpeed.pluse_send>=add_pluse\
					&& MotorAddSpeed.Add_Minus==MINUS && MotorAddSpeed.Add_Cnt>0		 )						//达到减速条件 减速阶段	 			
			{
//				u2_printf("2222222\t%d\r\n",MotorAddSpeed.pluse_send);//调试串口输出
				MotorAddSpeed.Add_Cnt--;
				Next_F 		 =	START_F+(MotorAddSpeed.Add_Cnt*ADD_SPEED);
				MotorAddSpeed.Arr_tim4_start	=	TIMER_F/Next_F;
				add_pluse 	+= T_ADD*Next_F/1000;							//计算出下次需要减速时的累计脉冲值
				TIM4->ARR	 = MotorAddSpeed.Arr_tim4_start-1;					
			}
			
			else if(Next_F==OBJ_F && MotorAddSpeed.pluse_send < pluse-(NEED_PLUSE/2))	//匀速阶段
			{}
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

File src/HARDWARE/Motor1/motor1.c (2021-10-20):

#include "motor1.h"
#include "sys.h"
#include "math.h"
#include "rs485.h"
//丝杠步进电机驱动程序	
//修改日期:2020/03/29
//版本：V2.0

/**********丝杠驱动器 端口定义 **************
//DRIVER1_DIR   PE3   丝杠方向
//DRIVER1_OE    PE4   丝杠驱动器使能
//STEP_PULSE1   PE11(TIM1_CH2)  丝杠驱动器脉冲
******************************************/

//系统加减速参数
speedRampData1 srd1;
//记录步进电机的位置
int stepPosition1 = 0;
//系统电机、串口状态
struct GLOBAL_FLAGS1 status1 = {FALSE, FALSE,TRUE};
unsigned static int a1=0;
unsigned static int d1=0;

void Driver1_Init(void)  //驱动器控制信号线初始化  使能 顺时针方向
{
	/***** 丝杠驱动器控制信号线初始化*******/     //PE3 方向  PE4 使能
	GPIO_InitTypeDef  GPIO_InitStructure;
	RCC_AHB1PeriphClockCmd(RCC_AHB1Periph_GPIOE, ENABLE); //使能GPIOE时钟
	
	GPIO_InitStructure.GPIO_Pin=GPIO_Pin_3|GPIO_Pin_4;//DRIVER2_DIR DRIVER2_OE对应引脚PE5 PE6
	GPIO_InitStructure.GPIO_Mode=GPIO_Mode_OUT;       //普通输出模式
	GPIO_InitStructure.GPIO_Speed=GPIO_Speed_100MHz;  //100M
	GPIO_InitStructure.GPIO_OType=GPIO_OType_PP;      //推挽输出
	GPIO_InitStructure.GPIO_PuPd=GPIO_PuPd_UP;        //上拉
	GPIO_Init(GPIOE, &GPIO_InitStructure);  //初始化GPIOE
	
	
	GPIO_SetBits(GPIOE,GPIO_Pin_3); //PE3输出高 顺时针方向  DRIVER1_DIR
	GPIO_ResetBits(GPIOE,GPIO_Pin_4); //PE4输出低 使能输出  DRIVER1_OE
	
}
/***********************************************
//TIM1_CH2(PE11) 单脉冲输出+重复计数功能初始化 
//TIM1 时钟频率 84*2=168MHz
//arr:自动重装值
//psc:时钟预分频数
************************************************/
void TIM1_OPM_RCR_Init(u16 arr,u16 psc)
{
	GPIO_InitTypeDef GPIO_InitStructure;
	TIM_TimeBaseInitTypeDef  TIM_TimeBaseStructure;
	TIM_OCInitTypeDef  TIM_OCInitStructure;
	NVIC_InitTypeDef NVIC_InitStructure;
	
	RCC_APB2PeriphClockCmd(RCC_APB2Periph_TIM1,ENABLE);  	//TIM1时钟使能  
	RCC_AHB1PeriphClockCmd(RCC_AHB1Periph_GPIOE, ENABLE); 	//使能PORTE时钟	
	
	/* GPIOE11复用为定时器1  */
	GPIO_InitStructure.GPIO_Pin=GPIO_Pin_11;           //TIM1_ch2对应IO口GPIOE11
	GPIO_InitStructure.GPIO_Mode=GPIO_Mode_AF;        //复用功能
	GPIO_InitStructure.GPIO_Speed=GPIO_Speed_100MHz;  //100M
	GPIO_InitStructure.GPIO_OType=GPIO_OType_PP;      //推挽复用输出
	GPIO_InitStructure.GPIO_PuPd=GPIO_PuPd_DOWN;      //下拉             为什么是下拉？
	GPIO_Init(GPIOE, &GPIO_InitStructure);  //初始化GPIOE11
	
	GPIO_PinAFConfig(GPIOE,GPIO_PinSource11,GPIO_AF_TIM1); //GPIOE11复用为定时器1
	
	/* 初始化定时器1  */
	TIM_TimeBaseStructInit(&TIM_TimeBaseStructure);
	
	TIM_TimeBaseStructure.TIM_Prescaler=psc; //预分频系数：设置用来作为TIMx时钟频率除数的预分频值 定时器实际时钟频率为：168MHz/（psc+1）
	TIM_TimeBaseStructure.TIM_CounterMode=TIM_CounterMode_Up;//TIM向上计数模式
	TIM_TimeBaseStructure.TIM_Period=arr;//自动重装载值
	TIM_TimeBaseStructure.TIM_ClockDivision=TIM_CKD_DIV1; //设置时钟分割 TIM_CKD_DIV1=0
	
	TIM_TimeBaseInit(TIM1, &TIM_TimeBaseStructure); //初始化TIM1	
	
	TIM_ClearITPendingBit(TIM1,TIM_IT_Update);//清除定时器TIM1的中断TIM_IT标志位
	TIM_UpdateRequestConfig(TIM1,TIM_UpdateSource_Regular); /********* 设置只有计数溢出作为更新中断 ********/
	TIM_SelectOnePulseMode(TIM1,TIM_OPMode_Single);/******* 单脉冲模式 **********/
	
	/*初始化TIM1的通道2*/
	TIM_OCInitStructure.TIM_OCMode=TIM_OCMode_PWM2; //选择定时器模式:TIM脉冲宽度调制模式2
	TIM_OCInitStructure.TIM_OCPolarity = TIM_OCPolarity_High; //输出极性:TIM输出比较极性高,,PWM波的起始电平为高
	TIM_OCInitStructure.TIM_OutputState=TIM_OutputState_Enable;//比较输出2使能
	TIM_OCInitStructure.TIM_OutputNState = TIM_OutputNState_Disable; /****** 比较输出2N失能????? *******/
	TIM_OCInitStructure.TIM_Pulse = arr>>1; // PWM的比较值：设置待装入捕获比较寄存器的脉冲值
	TIM_OC2Init(TIM1, &TIM_OCInitStructure);  //根据TIM_OCInitStruct中指定的参数初始化外设TIM1的通道2
	
	TIM_OC2PreloadConfig(TIM1, TIM_OCPreload_Enable);  //TIM1的CH2预装载使能
	TIM_ARRPreloadConfig(TIM1, ENABLE); //使能TIM1在ARR上的预装载寄存器
	
	/*初始化TIM1中断*/
	TIM_ITConfig(TIM1, TIM_IT_Update ,ENABLE);  //TIM1使能或者失能指定的TIM中断函数
	
	NVIC_InitStructure.NVIC_IRQChannel=TIM1_UP_TIM10_IRQn;  //TIM1更新中断;  NVIC_IRQChannel确定是哪一个中断
	NVIC_InitStructure.NVIC_IRQChannelPreemptionPriority= 1;//抢占优先级1级  NVIC_IRQChannelPreemptionPriority抢占优先级
	NVIC_InitStructure.NVIC_IRQChannelSubPriority= 1;// 响应优先级1级        NVIC_IRQChannelSubPriority响应优先级
	NVIC_InitStructure.NVIC_IRQChannelCmd=ENABLE;//IRQ通道被使能
	NVIC_Init(&NVIC_InitStructure);  //根据NVIC_InitStruct中指定的参数初始化外设NVIC寄存器
	
	TIM_ClearITPendingBit(TIM1, TIM_IT_Update);  //清除TIM1的中断待处理位:TIM 中断源
	TIM_Cmd(TIM1, ENABLE);  //使能TIM1
	
	
}	

void MSD_ENA1(FunctionalState NewState)
{
    if(NewState)
    {
      //ENA失能，禁止驱动器输出
      GPIO_SetBits(GPIOE,GPIO_Pin_4);
      //紧急停止标志位为真
      status1.out_ena = FALSE; 
      //printf("\n\r驱动器禁止输出（脱机状态）此时电机为无保持力矩状态，可以手动旋转电机");        
    }
    else
    {
      //ENA使能
      GPIO_ResetBits(GPIOE,GPIO_Pin_4);
      //紧急停止标志位为假
      status1.out_ena = TRUE; 
      //printf("\n\r驱动器恢复运行，此时电机为保持力矩状态，此时串口指令可以正常控制电机");         
    }
    
}

/*! \brief 以给定的脉冲数移动步进电机
 *  通过计算加速到最大速度，以给定的脉冲数开始减速
 *  如果加速度和减速度很小，步进电机会移动很慢，还没达到最大速度就要开始减速
 *  \param step   移动的脉冲数 (正数为顺时针，负数为逆时针).
 *  \param accel  加速度,如果取值为10，10Hz/脉冲
 *  \param decel  减速度,如果取值为10，10Hz/脉冲
 *  \param speed  最大频率,如果取值为100,最大频率100Hz
 */
void MSD_Move1(signed int step, unsigned int accel, unsigned int decel, unsigned int speed)
{
	//达到最大速度时的脉冲数.
    unsigned int max_s_lim;
    //必须开始减速的脉冲数(如果还没加速到达最大速度时)。
    unsigned int accel_lim;
	
	a1=accel;
	d1=decel;

    // 根据脉冲数的正负来判断方向
    if(step < 0)//逆时针
    {
        //srd.dir = CCW;
		GPIO_ResetBits(GPIOE,GPIO_Pin_3);
        step = -step;
    }
    else//顺时针
    {
        GPIO_SetBits(GPIOE,GPIO_Pin_3); //PE3输出高 顺时针方向  DRIVER2_DIR
		//srd.dir = CW;
    }
    // 输出电机方向
    //DIR(srd.dir);
    // 配置电机为输出状态
    //status.out_ena = TRUE;
    
    // 如果只移动一步
    if(step == 1)
    {
        // 只移动一步
        srd1.accel_count = -1;
        // 减速状态
        srd1.run_state = DECEL;
        // 短延时
        srd1.step_delay = 20;
        // 配置电机为运行状态
        status1.running = TRUE;
        //设置定时器重装值	
        TIM_SetAutoreload(TIM1,srd1.step_delay);
        //设置占空比为50%	
        TIM_SetCompare2(TIM1,srd1.step_delay>>1);
        //使能定时器	      
        TIM_Cmd(TIM1, ENABLE); 
     }
    // 步数不为零才移动
    else if(step != 0)
    {
   
    // 设置最大速度极限, 计算得到min_delay用于定时器的计数器的值。
    srd1.min_delay = 1000000/speed-1;

    srd1.step_delay = 1000000/20-1;  //f1=20Hz；
		
    // 计算多少脉冲之后达到最大速度的限制
    // max_s_lim = speed^2 / (2*alpha*accel)
    max_s_lim = (((long)(speed-20)/(long)(accel))+1);
		
    // 如果达到最大速度小于0.5个脉冲，我们将四舍五入为0
    // 但实际我们必须移动至少一个脉冲才能达到想要的速度
    if(max_s_lim == 0)
    {
        max_s_lim = 1;
    }

    // 计算多少脉冲之后我们必须开始减速（因为还有减速），由三角形面积即可计算出
    // n1 = (n1+n2)decel / (accel + decel)
    accel_lim = ((long)step*decel) / (accel+decel)-1;
    // 我们必须加速至少1个脉冲才能才能开始减速.
    if(accel_lim == 0)
    {
        accel_lim = 1;
    }
    // 使用限制条件计算出减速所用的脉冲数（负数表示）
    //srd.decel_val为负数
    if(accel_lim <= max_s_lim)//三角形的情况
    {
        srd1.decel_val = accel_lim - step;
    }
    else//梯形的情况
    {
        srd1.decel_val = -(((long)(speed-20)/(long)(decel))+1);
    }
    // 当只剩下一步我们必须减速
    if(srd1.decel_val == 0)
    {
        srd1.decel_val = -1;
    }
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
